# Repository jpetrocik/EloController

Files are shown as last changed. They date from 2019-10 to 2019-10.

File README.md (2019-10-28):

EloController is an open source  replacement for the controller for your eBike. The project was created simply out of a hobbyist interest. The goal of the project is to get to a point where the controller achieves the goal set out below.    

The design separates the main logic, aka BCU, and brushless DC driver.  Many semiconductor manufacturers are now creating dedicated chip for brushless dc motor controlling, so instead of focusing on trapezoidal, sinusoidal and field-oriented control software let a dedicate chip handle that, and with the time saved spent making the users experience better. Currently, the board uses the JYQD DC Brushless Motor Controller as a daughter board for controlling the motor.  This board is available on eBay and Amazon for about $15.  The board is rated up to 500W when using a heat sink.

Unique to the EloController is the use of the HC-05 bluetooth module to provide connectivity between your smart phone and bike.  All important data is streamed to the phone using a messaging protocol, analogous to CANBus message, the system used by modern cars to connect all the different computer modules. The EloControler acts a the BCU, or Bike Control Unit similar to a modern car's ECU.  All peripheral plug into the BCU and the BCU stream data over bluetooth to your smart phone.  Information like bike speed, hub speed, brake on/off, battery level, etc are streamed and display on your phone, no need for a separate display on the the handle bars.  Additionally the phone can send message back to the BCU for configuration setting and for features like disabling the motor, equivalent to a digital lock.  

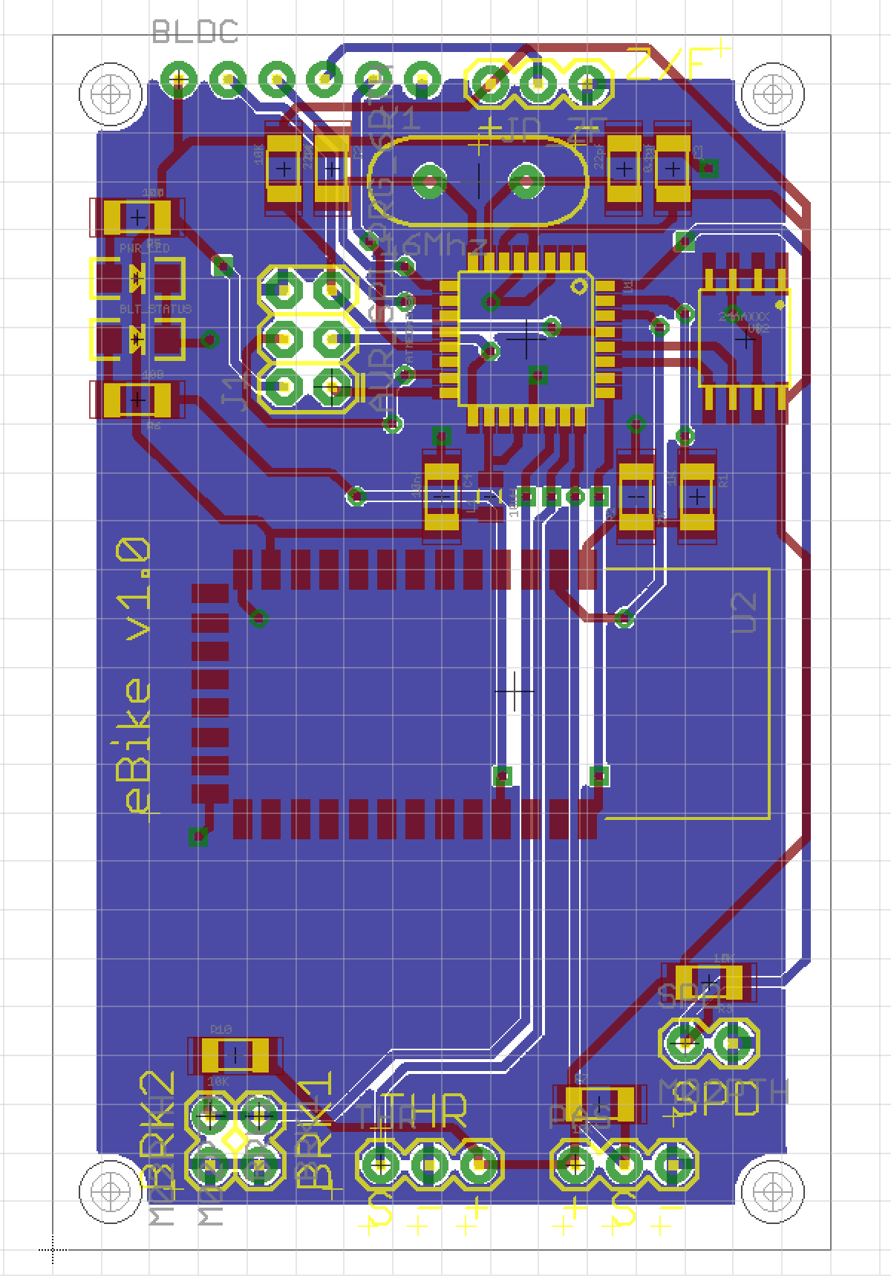
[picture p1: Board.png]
PCB Board


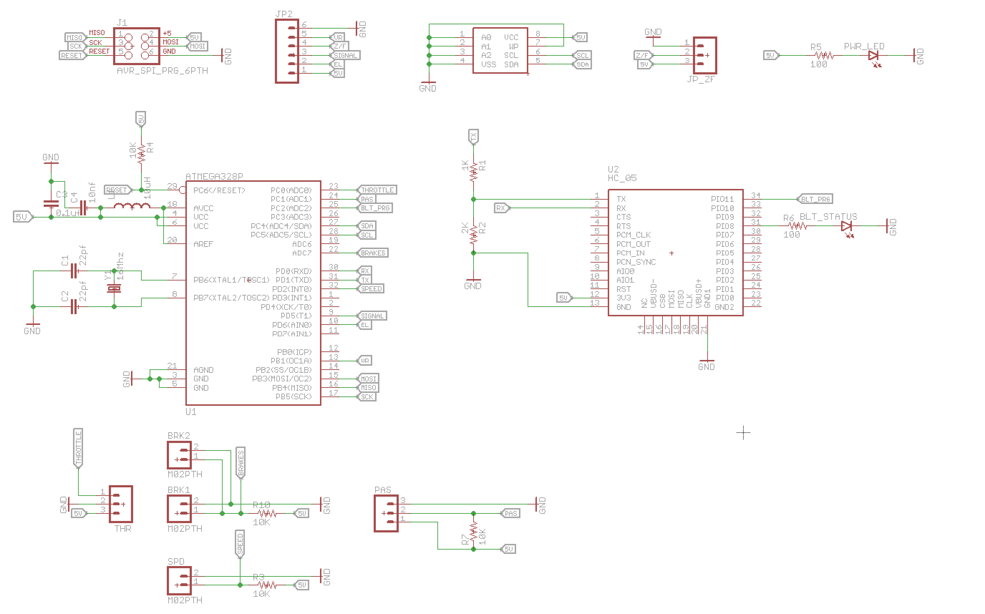
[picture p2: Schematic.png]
Schematic


Current Status:

* Individual modules are tested and the design is confirmed.
* PCB Design complete

Next Steps:
* Order PCB
* Solder up PCB
* Install and Test

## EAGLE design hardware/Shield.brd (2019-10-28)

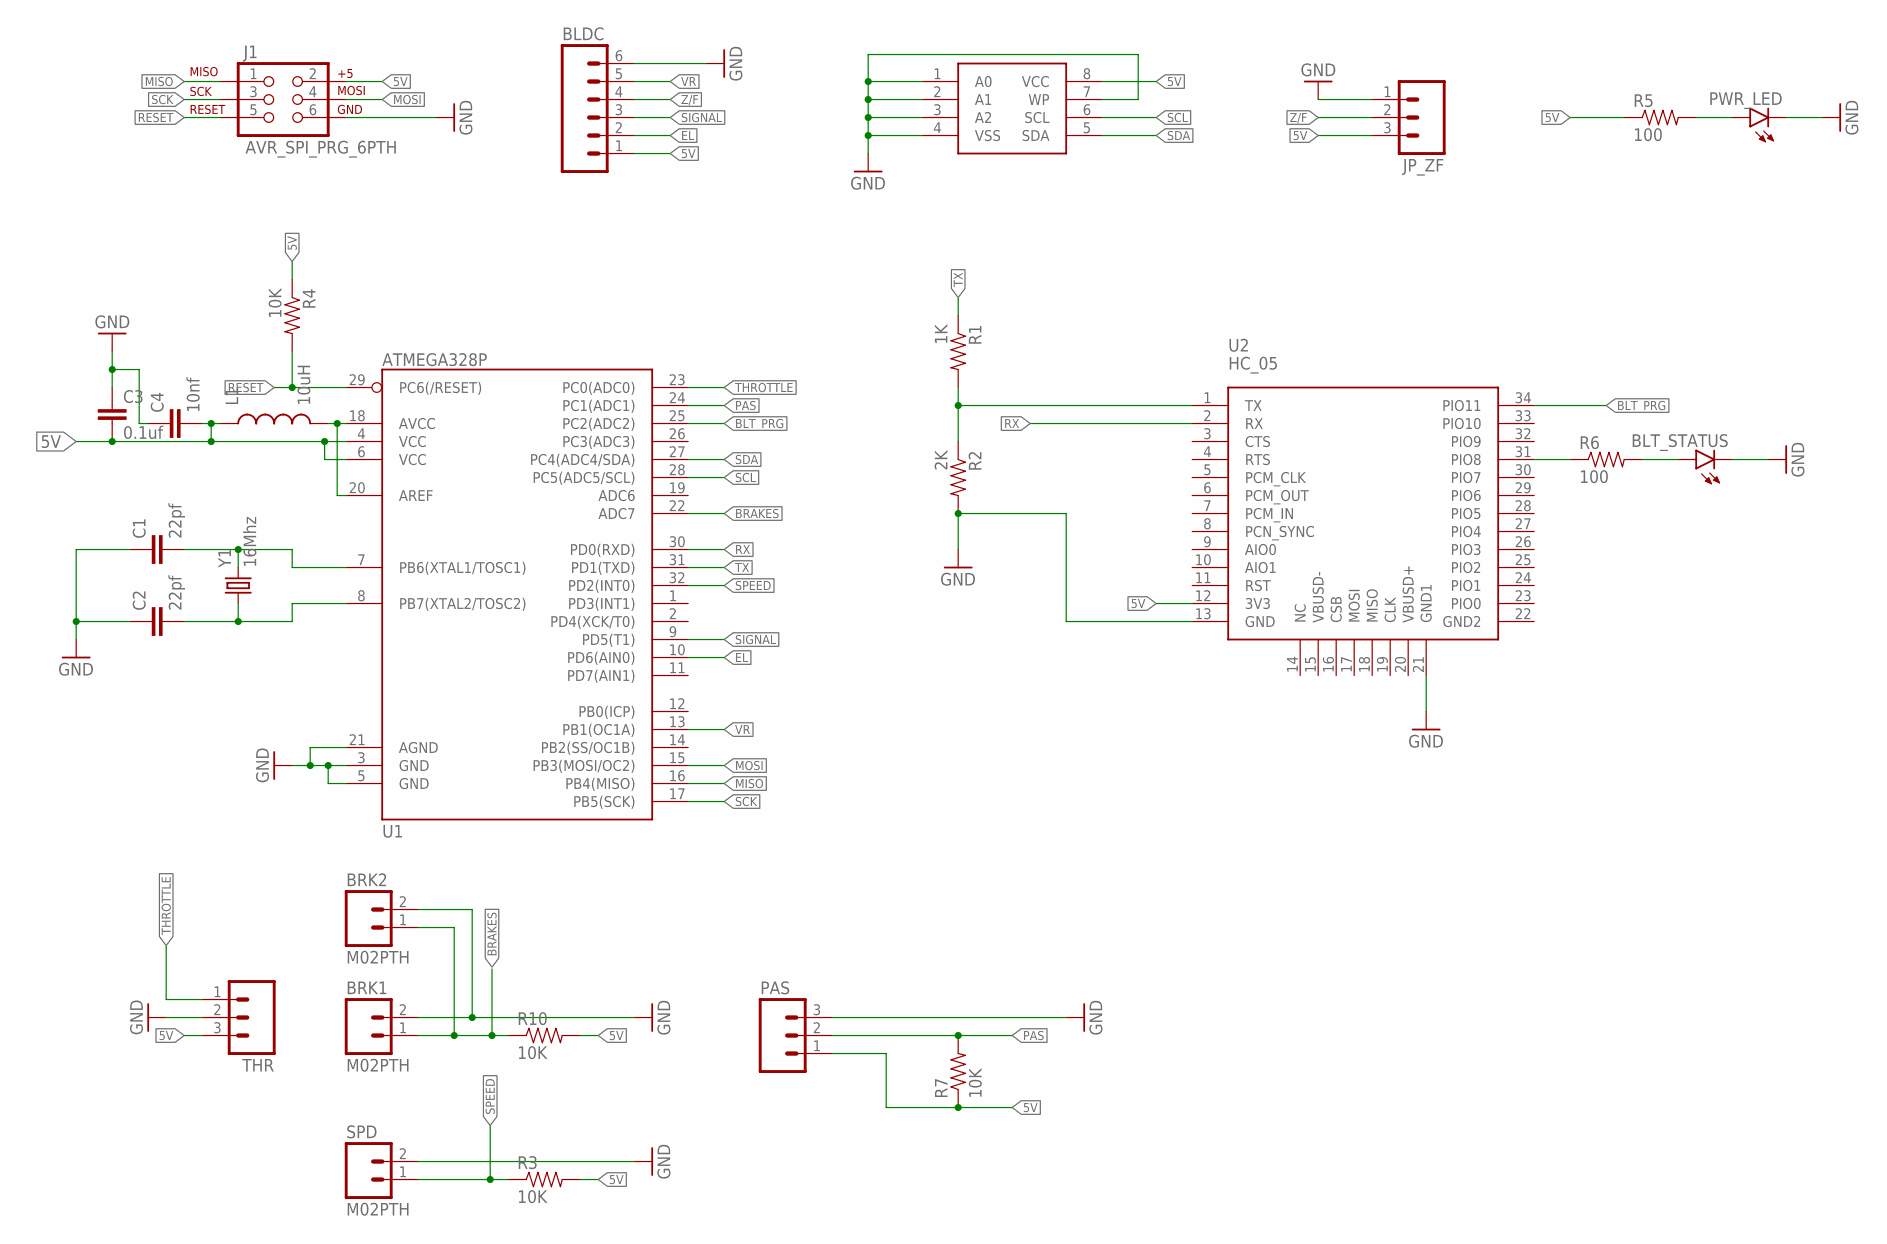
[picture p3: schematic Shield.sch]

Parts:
BLDC: M06NO_SILK_FEMALE_PTH; 1X06_NO_SILK
BLT_STATUS: LED1206; LED-1206
BRK1, BRK2: M02PTH; 1X02
C1, C2: 22pf; 1206
C3: 0.1uf; 1206
C4: 10nf; 1206
J1: AVR_SPI_PRG_6PTH; 2X3
JP_ZF: M03PTH; 1X03
L1: 10uH; 0805
PAS: M03PTH; 1X03
PWR_LED: LED1206; LED-1206
R1: 1K; 1206
R2: 2K; 1206
R3, R4, R7, R10: 10K; 1206
R5, R6: 100; 1206
SPD: M02PTH; 1X02
THR: M03PTH; 1X03
U1: ATMEGA328P; TQFP32-08
U2: HC_05; BLUETOOTH_SMD
U$2: 24AAXXX; SOIC-8-EIAJ
Y1: 16Mhz; HC49US

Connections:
5V: BLDC.1, C3.2, C4.2, J1.2, JP_ZF.3, L1.1, PAS.1, R3.2, R4.1, R5.1, R7.1, R10.2, THR.3, U1.4 (VCC), U1.6 (VCC), U2.12 (3V3), U$2.8 (VCC)
BLT_PRG: U1.25 (PC2(ADC2)), U2.34 (PIO11)
BRAKES: BRK1.1, BRK2.1, R10.1, U1.22 (ADC7)
EL: BLDC.2, U1.10 (PD6(AIN0))
GND: BLDC.6, BLT_STATUS.C, BRK1.2, BRK2.2, C1.1, C2.1, C3.1, C4.1, J1.6, JP_ZF.1, PAS.3, PWR_LED.C, R2.2, SPD.2, THR.2, U1.3 (GND), U1.5 (GND), U1.21 (AGND), U2.13 (GND), U2.21 (GND1), U$2.1 (A0), U$2.2 (A1), U$2.3 (A2), U$2.4 (VSS), U$2.7 (WP)
MISO: J1.1, U1.16 (PB4(MISO))
MOSI: J1.4, U1.15 (PB3(MOSI/OC2))
unnamed: R1.2, R2.1, U2.1 (TX)
unnamed: PWR_LED.A, R5.2
unnamed: R6.1, U2.31 (PIO8)
unnamed: BLT_STATUS.A, R6.2
unnamed: L1.2, U1.18 (AVCC), U1.20 (AREF)
unnamed: C1.2, U1.7 (PB6(XTAL1/TOSC1)), Y1.2
unnamed: C2.2, U1.8 (PB7(XTAL2/TOSC2)), Y1.1
PAS: PAS.2, R7.2, U1.24 (PC1(ADC1))
RESET: J1.5, R4.2, U1.29 (PC6(/RESET))
RX: U1.30 (PD0(RXD)), U2.2 (RX)
SCK: J1.3, U1.17 (PB5(SCK))
SCL: U1.28 (PC5(ADC5/SCL)), U$2.6 (SCL)
SDA: U1.27 (PC4(ADC4/SDA)), U$2.5 (SDA)
SIGNAL: BLDC.3, U1.9 (PD5(T1))
SPEED: R3.1, SPD.1, U1.32 (PD2(INT0))
THROTTLE: THR.1, U1.23 (PC0(ADC0))
TX: R1.1, U1.31 (PD1(TXD))
VR: BLDC.5, U1.13 (PB1(OC1A))
Z/F: BLDC.4, JP_ZF.2

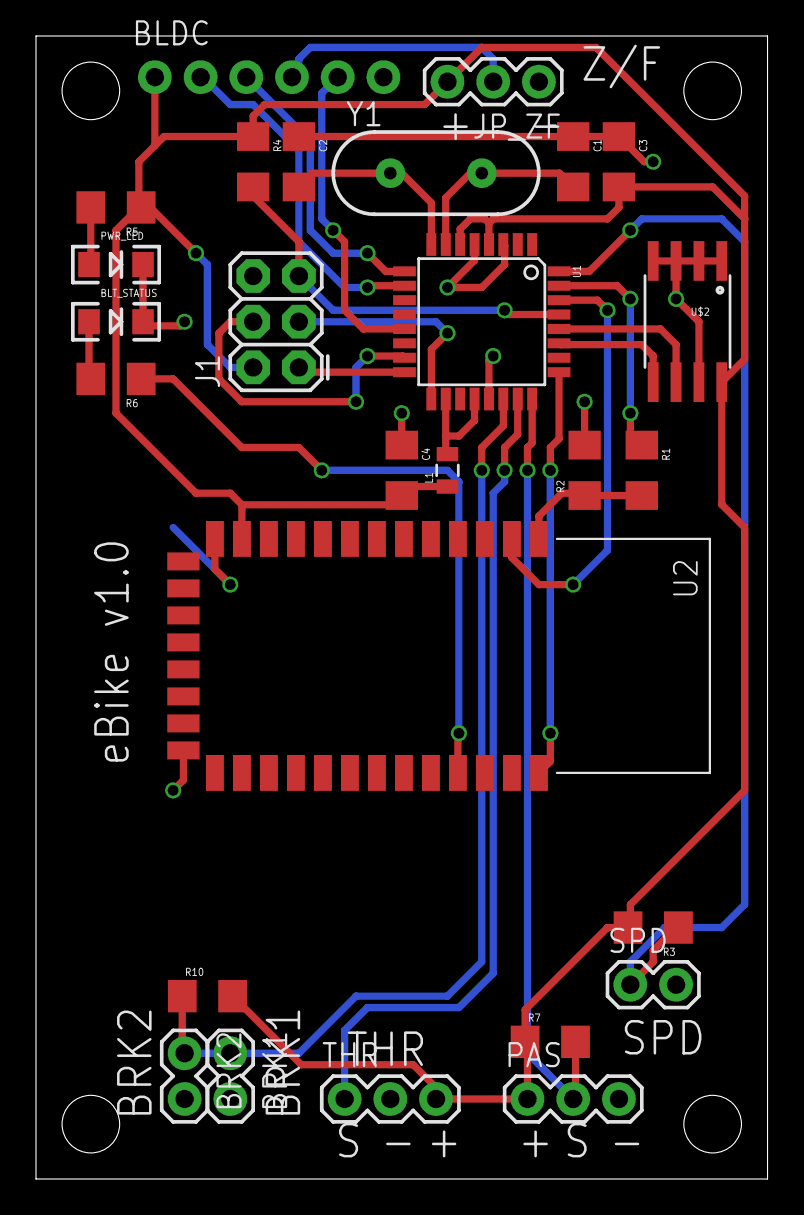
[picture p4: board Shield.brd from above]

Board: 2 copper layers, 40.6 x 63.5 mm, 27 parts (0 on the bottom side), 26 nets.

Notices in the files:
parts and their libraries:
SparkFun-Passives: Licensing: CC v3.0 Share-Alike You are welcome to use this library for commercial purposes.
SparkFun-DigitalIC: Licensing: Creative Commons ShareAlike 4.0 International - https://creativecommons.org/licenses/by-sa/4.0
